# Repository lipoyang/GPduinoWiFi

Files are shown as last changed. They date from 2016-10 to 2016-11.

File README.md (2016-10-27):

GPduino WiFi
=========

## 概要
GPduino WiFiは、ESP8266搭載のWiFiラジコン制御ボードです。  
GPduinoに関する詳細は、[GPduinoサポートページ](http://lipoyang.net/gpduino)をごらんください。  
GPduinoWiFiの回路/基板設計データとプリセットファームウェアのソースをここに公開します。

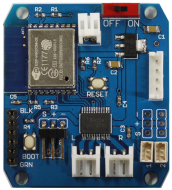
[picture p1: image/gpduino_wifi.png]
GPduinoWiFiの写真
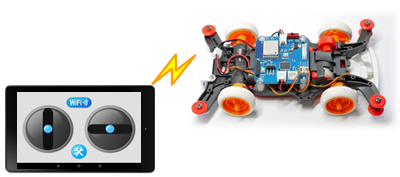
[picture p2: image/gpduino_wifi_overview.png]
概要の図
　　　　　

## ファイル一覧

* firm/GPduinoWiFi/ : ファームウェア(ESP8266のArduinoスケッチ)
* hard/GPduinoWiFi/
	* GPduinoWiFi.sch/brd: 回路/基板設計データ(Eagle形式)
	* GPduinoWiFi.pdf: 回路図(PDF)
	* GPduinoWiFi_BOM.xlsx: BOMリスト(Excel形式)
	* GPduinoWiFi.GBL/GBO/GBP/GBS/GML/GTL/GTO/GTP/GTS/TXT: ガーバデータ
* LICENSE: Apache Licence 2.0です。
	* ただし、回路/基板設計は、Creative Commons Attribution Share-Alike 3.0です。
* README.md これ

## ファームウェアの書き込み
GPduino WiFi はESP8266を搭載しており、Arduinoでファームウェアを開発できます。

* 書き込みには、USBシリアル変換基板が必要です。CN11に接続してください。
	* SparkFun製 FTDI Basic Breakout - 3.3V を推奨します。かならず、3.3Vのものを使用してください。
* まず、ArduinoIDE をインストールしておきます。 (ここでは 1.6.9 を使用)
* [ファイル] > [環境設定] > [Additional Boards Manager URLs:]に下記URLをコピペ
	* http://arduino.esp8266.com/stable/package_esp8266com_index.json (安定版)
	* http://arduino.esp8266.com/staging/package_esp8266com_index.json (開発版)
* [ツール] > [ボード] > [ボードマネージャ] で [esp8266] をインストール
* [ツール] > [ボード] で [Generic ESP8266 Module]を選択
	* Flash Mode : QIO
	* Flash Frequency : 40MHz
	* Upload Using : Serial
	* CPU Frequency : 80MHz
	* Flash Size : 4M(3M SPIFFS)　(3MBをファイルシステムで使用 / 1MBをスケッチで使用)
	* Debug port : Disabled
	* Debug Level : None
	* Reset Method : nodemcu
	* Upload Speed : 115200
	* シリアルポート : USBシリアルのCOM番号
	* 書込装置 : USBasp
* BOOTボタン(SW3)を押し下げた状態で、RESETボタン(SW2)を押して離します。
* Uploadボタンで、ファームウェアを書き込みます。

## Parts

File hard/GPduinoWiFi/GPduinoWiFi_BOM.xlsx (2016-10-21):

GPduino WiFi BOM
基板本体
No | Reference | Part Number | Vender | Description | DNP | Qty | Unit Price | Price | Lot Size | Supplier | Supplier Code
1 | C1,2 | 47u(3216) | (generic) | 3216型 |  | 2 | 30 | 60 | 10 | 秋月 | P-06040
2 | C3,4,5 | 0.1u(1608) | (generic) | 1608型 |  | 3 | 0.325 | 0.975 | 4000 | 秋月 | P-01299
3 | CN1,2 | S2B-EH | JST | EH 2極 L型ポスト | DNP | 0 | 16 | 0 | 1 | 共立 | -
4 | CN3 | S2B-PH-K-S | JST | PH 2極 L型ポスト |  | 1 | 16 | 16 | 1 | 共立 | -
5 | CN4 | B4B-EH-A | JST | EH 4極 I型ポスト | DNP | 0 | 21 | 0 | 1 | 共立 | -
6 | CN5 | 53048-0310 | Molex | PicoBlade 3極 L型ポスト | DNP (部品は付属) | 1 | 45 | 45 | 5 | RS | 319-1092
7 | CN6,7 | 53047-0310 | Molex | PicoBlade 3極 I型ポスト | DNP | 0 | 29 | 0 | 5 | RS | 319-1064
8 | CN8 | - | (generic) | ピンヘッダ 3ピン | DNP (部品は付属) | 1 | 35 | 35 | 16 | 共立 | -
9 | CN9,10 | - | (generic) | ピンヘッダ 3ピン | DNP | 0 | 17 | 0 | 12 | 共立 | -
10 | CN11 | 0 | (generic) | ピンヘッダ 6ピン I型 | DNP (部品は付属) | 1 | 70 | 70 | 8 | 共立 | -
12 | R1 | 100k(1608) | (generic) | 1608型 |  | 1 | 0.2 | 0.2 | 2500 | 秋月 | R-06104
13 | R2,3,4,5,6,7 | 10k(1608) | (generic) | 1608型 |  | 6 | 0.2 | 1.2 | 2500 | 秋月 | R-06103
14 | SW1 | SS-12SDP2 | NKK | スライドスイッチ | DNP (部品は付属) | 1 | 66 | 66 | 1 | 共立 | 391139
15 | SW2,3 | SKRPACE010 | ALPS | 表面実装タクトスイッチ |  | 2 | 20 | 40 | 5 | 秋月 | P-06185
16 | U1 | TC1262-3.3VDB05MP | Microchip | LDO, 3.3V-0.5A, SOT-223型 |  | 1 | 81 | 81 | 1 | RS | 703-7905
17 | U2 | TB6621FNG | Toshiba | Dual DCモータドライバ |  | 1 | 306 | 306 | 1 | RS | 770-3797
18 | U3 | ESP-WROOM-02 | Espressif Systems | ESP8266 WiFiモジュール |  | 1 | 550 | 550 | 1 | 秋月 | M-09607
19 | - | - | Elecrow | 基板 |  | 1 | 275.1 | 275.1 | 10 | Elecrow | -
20 | - | PH2P300L | Marutsu | PH 2極 アッセンブルケーブル |  | 1 | 54 | 54 | 1 | マルツ | -
 |  |  |  |  |  |  | Total | 1600.475

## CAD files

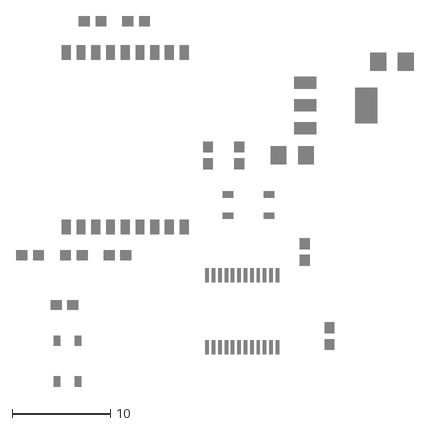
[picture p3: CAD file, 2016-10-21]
hard/GPduinoWiFi/GPduinoWiFi.dxf
40.4 x 37.7

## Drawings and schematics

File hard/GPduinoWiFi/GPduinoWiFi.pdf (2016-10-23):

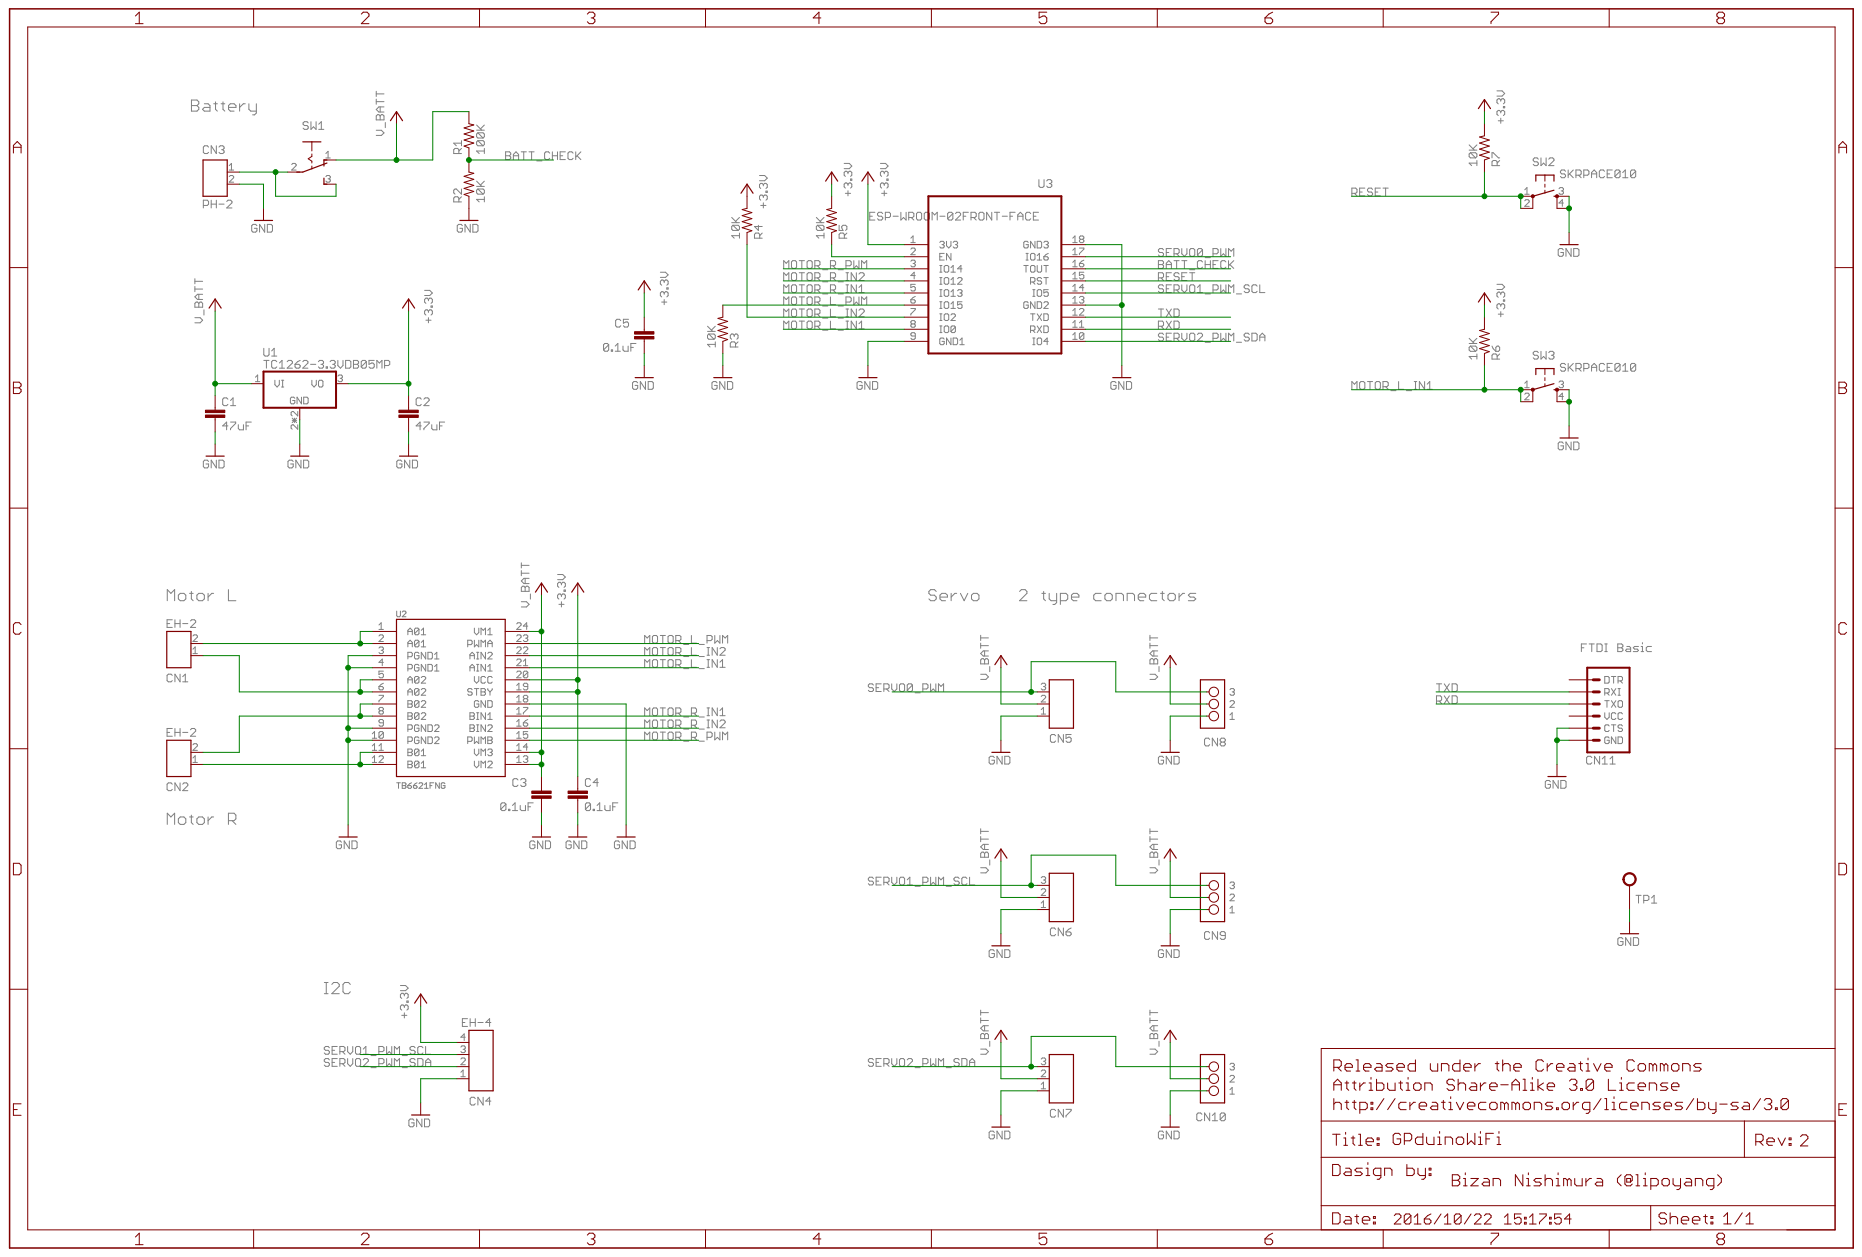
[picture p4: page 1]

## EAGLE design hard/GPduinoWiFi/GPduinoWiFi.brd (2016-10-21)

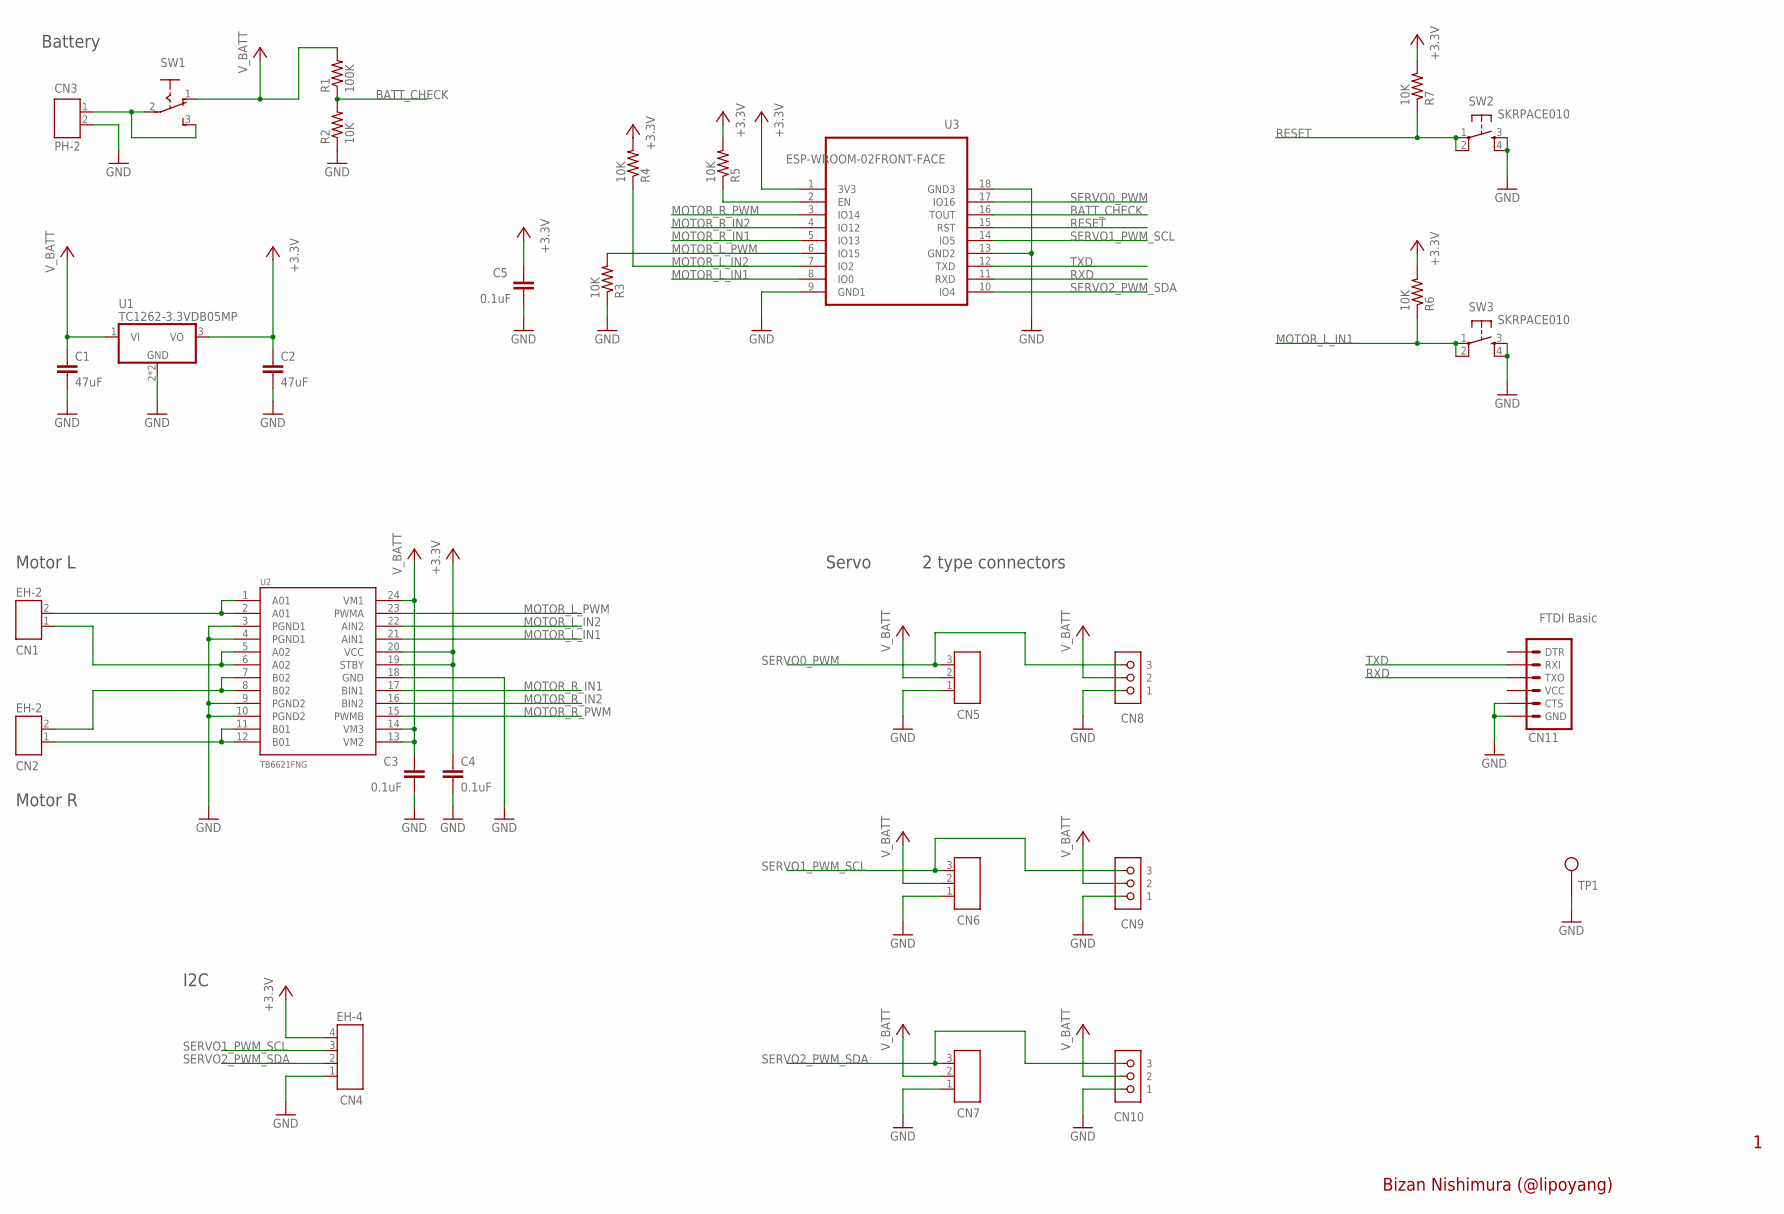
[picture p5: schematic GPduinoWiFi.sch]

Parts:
C1, C2: 47uF; C3216
C3, C4, C5: 0.1uF; C1608
CN1, CN2: EH-2
CN3: PH-2
CN4: EH-4
CN5, CN6, CN7: PICOBLADE-3
CN8, CN9, CN10: cn6; CON_RC_SERVO
CN11: FTDI Basic; 1X06
R1: 100K; 0603-RES
R2, R3, R4, R5, R6, R7: 10K; 0603-RES
SW1: SW1; SLIDE-SW
SW2, SW3: SKRPACE010
TP1: TEST_PIN
U1: TC1262-3.3VDB05MP; SOT223
U2: TB6621FNG; SSOP24
U3: ESP-WROOM-02FRONT-FACE; FRONT-FACE

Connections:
+3V3: C2.1, C4.1, C5.1, CN4.4, R4.2, R5.2, R6.2, R7.2, U1.3 (VO), U2.19 (STBY), U2.20 (VCC), U3.1 (3V3)
A01: CN1.2, U2.1 (A01), U2.2 (A01)
A02: CN1.1, U2.5 (A02), U2.6 (A02)
BATT_CHECK: R1.1, R2.2, U3.16 (TOUT)
GND: C1.2, C2.2, C3.2, C4.2, C5.2, CN3.2, CN4.1, CN5.1, CN6.1, CN7.1, CN8.1, CN9.1, CN10.1, CN11.5 (CTS), CN11.6 (GND), R2.1, R3.1, SW2.3, SW2.4, SW3.3, SW3.4, TP1.1, U1.2 (GND), U1.4 (GND), U2.3 (PGND1), U2.4 (PGND1), U2.9 (PGND2), U2.10 (PGND2), U2.18 (GND), U3.9 (GND1), U3.13 (GND2), U3.18 (GND3)
MOTOR_L_IN1: R6.1, SW3.1, SW3.2, U2.21 (AIN1), U3.8 (IO0)
MOTOR_L_IN2: R4.1, U2.22 (AIN2), U3.7 (IO2)
MOTOR_L_PWM: R3.2, U2.23 (PWMA), U3.6 (IO15)
MOTOR_R_IN1: U2.17 (BIN1), U3.5 (IO13)
MOTOR_R_IN2: U2.16 (BIN2), U3.4 (IO12)
MOTOR_R_PWM: U2.15 (PWMB), U3.3 (IO14)
unnamed: CN3.1, SW1.2, SW1.3 (S)
unnamed: R5.1, U3.2 (EN)
unnamed: CN2.1, U2.11 (B01), U2.12 (B01)
unnamed: CN2.2, U2.7 (B02), U2.8 (B02)
RESET: R7.1, SW2.1, SW2.2, U3.15 (RST)
RXD: CN11.3 (TXO), U3.11 (RXD)
SERVO0_PWM: CN5.3, CN8.3, U3.17 (IO16)
SERVO1_PWM_SCL: CN4.3, CN6.3, CN9.3, U3.14 (IO5)
SERVO2_PWM_SDA: CN4.2, CN7.3, CN10.3, U3.10 (IO4)
TXD: CN11.2 (RXI), U3.12 (TXD)
V_BATT: C1.1, C3.1, CN5.2, CN6.2, CN7.2, CN8.2, CN9.2, CN10.2, R1.2, SW1.1 (O), U1.1 (VI), U2.13 (VM2), U2.14 (VM3), U2.24 (VM1)

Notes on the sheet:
Battery
Servo
Motor L
Bizan Nishimura (@lipoyang)
2 type connectors
Motor R
I2C

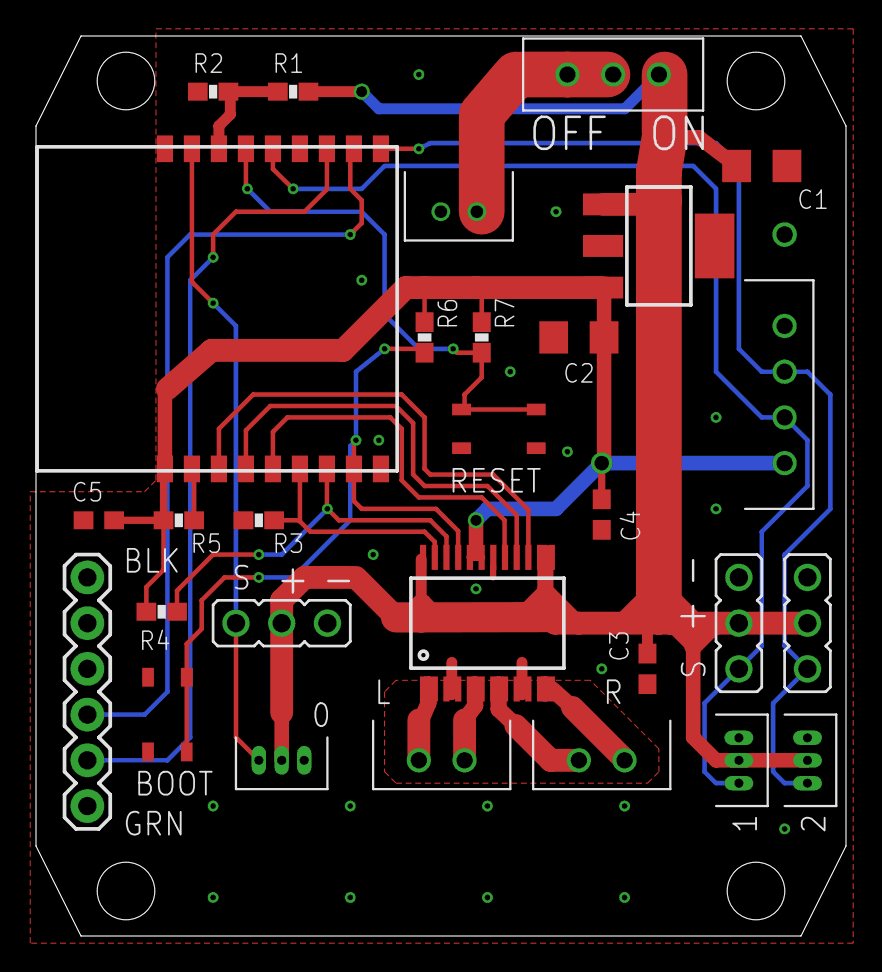
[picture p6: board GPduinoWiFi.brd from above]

Board: 2 copper layers, 45.0 x 50.0 mm, 30 parts (0 on the bottom side), 22 nets.

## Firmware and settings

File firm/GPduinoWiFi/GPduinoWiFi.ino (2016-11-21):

#include <Servo.h>
#include <EEPROM.h>
extern "C" {
#include "user_interface.h"
}
#include "common.h"
#include "MovingAverage.h"
#include "UdpComm.h"

// UDP通信クラス
UdpComm udpComm;
// UDP受信コールバック
void udpComm_callback(char* buff);

// ピン番号 (デジタル)
#define MOTOR_R_PWM    14
#define MOTOR_R_IN2    12
#define MOTOR_R_IN1    13
#define MOTOR_L_PWM    15
#define MOTOR_L_IN2    2
#define MOTOR_L_IN1    0
#define SERVO0_PWM     16
#define SERVO1_PWM     5
#define SERVO2_PWM     4

// サーボ
Servo servo[3];

// バッテリー電圧チェック
MovingAverage Vbat_MovingAve;

// モード
static int drive_mode;
#define MODE_TANK   0   // 戦車モード
#define MODE_CAR    1   // 自動車モード

// 戦車モードのプロポ状態保持用
static int g_fb;  // 前後方向
static int g_lr;  // 左右方向

// 暴走チェックカウンタ
static int cnt_runaway;

// 3.5V未満でローバッテリーとする
// (3.5V / 11) / 1.0V * 1024 =  325
#define LOW_BATTERY    325

// 四輪操舵のモード
static int g_steer_pol_f;
static int g_steer_pol_b;

// サーボの調整
static int g_servo_pol[3]; // 極性
static int g_servo_ofs[3]; // オフセット
static int g_servo_amp[3]; // 振幅

// 送信バッファ
static char txbuff[256];

/**
 * バッテリー電圧チェック
 */
void battery_check()
{
    if(!udpComm.isReady()) return;
    
    static int cnt1 = 0;
    static int cnt2 = 0;
    
    // 100msecごとに電圧値測定
    cnt1++;
    if(cnt1 < 100) return;
    cnt1 = 0;

    unsigned short Vbat = system_adc_read();
    unsigned short Vbat_ave = Vbat_MovingAve.pop(Vbat);
    //Serial.print("Vbat_ave");Serial.println(Vbat_ave);

    // 1秒ごとに電圧値送信
    cnt2++;
    if(cnt2 >= 10)
    {
        cnt2=0;
        
        txbuff[0]='#';
        txbuff[1]='B';
        Uint16ToHex(&txbuff[2], Vbat_ave, 3);
        txbuff[5]='$';
        txbuff[6]='\0';
        udpComm.send(txbuff);
    }
    
    // 電圧が低下したら停止
    if(Vbat_ave < LOW_BATTERY){
        // モータ停止
        analogWrite(MOTOR_L_PWM, 0);
        analogWrite(MOTOR_R_PWM, 0);
        digitalWrite(MOTOR_L_IN1, LOW);
        digitalWrite(MOTOR_L_IN2, LOW);
        digitalWrite(MOTOR_R_IN1, LOW);
        digitalWrite(MOTOR_R_IN2, LOW);
        // 復帰しない
        while(true){
            ;
        }
    }
}

/**
 * 暴走チェック
 */
void runaway_check()
{
    cnt_runaway++;
    
    // 1秒間コマンドが来なければモータ停止
    if(cnt_runaway > 1000)
    {
      analogWrite(MOTOR_L_PWM, 0);
      analogWrite(MOTOR_R_PWM, 0);
      digitalWrite(MOTOR_L_IN1, LOW);
      digitalWrite(MOTOR_L_IN2, LOW);
      digitalWrite(MOTOR_R_IN1, LOW);
      digitalWrite(MOTOR_R_IN2, LOW);
    }
}

/*
 * サーボの初期化, モードの設定
 */
void servo_init()
{
    int i;
    if(EEPROM.read(0) == 0xA5){
        for(i=0;i<3;i++){
            g_servo_pol[i] = (int)((signed char)EEPROM.read(i*3 + 1));
            g_servo_ofs[i] = (int)((signed char)EEPROM.read(i*3 + 2));
            g_servo_amp[i] =                    EEPROM.read(i*3 + 3);
        }
        drive_mode = EEPROM.read(10);
        if(drive_mode == MODE_TANK){
            Serial.println("TANK MODE");
        }else{
            Serial.println("CAR MODE");
        }
        
    }else{
        EEPROM.write(0, 0xA5);
        for(i=0;i<3;i++){
            g_servo_pol[i] = 1;
            g_servo_ofs[i] = 0;
            g_servo_amp[i] = 90;
            EEPROM.write(i*3 + 1, g_servo_pol[i]);
            EEPROM.write(i*3 + 2, g_servo_ofs[i]);
            EEPROM.write(i*3 + 3, g_servo_amp[i]);
        }
        drive_mode = MODE_CAR;
        EEPROM.write(10, drive_mode);
        EEPROM.commit();
    }
    servo[0].attach(SERVO0_PWM);
    servo[1].attach(SERVO1_PWM);
    servo[2].attach(SERVO2_PWM);
    servo_ctrl(0,0);
    servo_ctrl(1,0);
    servo_ctrl(2,0);
}

/*
 * サーボ制御
 */
void servo_ctrl(int ch, int val)
{
    int deg = 90 + ((val + g_servo_ofs[ch]) *  g_servo_amp[ch]) / 127 * g_servo_pol[ch];
    
    // sprintf(txbuff, "%4d %4d / %4d %4d %4d", val, deg, g_servo_ofs[ch], g_servo_amp[ch], g_servo_pol[ch]);
    // Serial.println(txbuff);
    
    servo[ch].write(deg);
}

// 初期設定
void setup() {
    Serial.begin(115200);
    delay(100);
    
    // EEPROMの初期化
    EEPROM.begin(128); // 128バイト確保
    
    // UDP通信の設定
    udpComm.beginAP(NULL, "12345678");
    //udpComm.beginSTA("SSID", "password", "gpduino");
    udpComm.onReceive = udpComm_callback;

    // PWMの初期化
    analogWrite(MOTOR_L_PWM, 0);
    analogWrite(MOTOR_R_PWM, 0);
    
    // GPIOの初期化
    digitalWrite(MOTOR_L_IN1, LOW);
    digitalWrite(MOTOR_L_IN2, LOW);
    digitalWrite(MOTOR_R_IN1, LOW);
    digitalWrite(MOTOR_R_IN2, LOW);
    pinMode(MOTOR_L_IN1, OUTPUT);
    pinMode(MOTOR_L_IN2, OUTPUT);
    pinMode(MOTOR_R_IN1, OUTPUT);
    pinMode(MOTOR_R_IN2, OUTPUT);
    
    // モード判定
    //int mode_check = analogRead( MODE_CHECK );
    //drive_mode = (mode_check > 512) ? MODE_CAR : MODE_TANK;
    
    //if(drive_mode == MODE_CAR){
        // サーボの初期化, モード設定
        servo_init();
    //}
    
    // 変数初期化
    g_fb = 0;
    g_lr = 0;
    cnt_runaway = 0;
    Vbat_MovingAve.init();
    g_steer_pol_f = 1;
    g_steer_pol_b = 0;
}

// メインループ
void loop() {
    
    // UDP通信
    udpComm.loop();
    // バッテリー電圧チェック
    battery_check();
    // 暴走チェック
    runaway_check();
    
    delay(1);
}

/*
 * モータの制御
 */
void ctrl_motor(int ch, int val)
{
    static const int IN1[]={MOTOR_L_IN1, MOTOR_R_IN1};
    static const int IN2[]={MOTOR_L_IN2, MOTOR_R_IN2};
    static const int PWM[]={MOTOR_L_PWM, MOTOR_R_PWM};
    
    int l,r;
    int lpwm,rpwm,lin1,lin2,rin1,rin2;
    
    int pwm = (abs(val) << 1) + 1;
    if(pwm<0) pwm = 0;
    if(pwm>255) pwm = 255;
    
    int in1,in2;
    if(val > 0){
        in1 = LOW;
        in2 = HIGH;
    }else if(val < 0){
        in1 = HIGH;
        in2 = LOW;
    }else{
        in1 = LOW;
        in2 = LOW;
        pwm = 0;
    }

    digitalWrite(IN1[ch], in1);
    digitalWrite(IN2[ch], in2);
    analogWrite(PWM[ch], pwm*4);
}

/**
 * 戦車のモータ制御
 */
void ctrl_tank()
{
    int l,r;
    int lpwm,rpwm,lin1,lin2,rin1,rin2;
    
    r = (int)(g_fb - g_lr/2);
    l = (int)(g_fb + g_lr/2);
    
    // sprintf(txbuff, "%4d %4d %4d %4d", l, r, g_fb, g_lr);
    // Serial.println(txbuff);
    
    ctrl_motor(0, l);
    ctrl_motor(1, r);
}

/**
 * 受信したコマンドの実行
 *
 * @param buff 受信したコマンドへのポインタ
 */
void udpComm_callback(char* buff)
{
    unsigned short val;
    int sval, sval2;
    int deg;
    int ch;
    int i;
    
    cnt_runaway = 0; // 暴走チェックカウンタのクリア
    
    Serial.print("udpComm_callback:");Serial.println(buff);
    
    if(buff[0] != '#') return;
    buff++;
    
    switch(buff[0])
    {
    /* Dコマンド(前進/後退)
       書式: #Dxx$
       xx: 0のとき停止、正のとき前進、負のとき後退。
     */
    case 'D':
        // 値の解釈
        if( HexToUint16(&buff[1], &val, 2) != 0 ) break;
        sval = (int)((signed char)val);
        
        // 自動車モードの場合
        if(drive_mode == MODE_CAR)
        {
            ctrl_motor(0, sval);
            ctrl_motor(1, sval);
        }
        // 戦車モードの場合
        else
        {
            g_fb = sval;
            ctrl_tank();
        }
        break;
        
    /* Tコマンド(旋回)
       書式: #Txxn$
       n: 4WSモード。0のとき後輪固定、1のとき同相、2のとき逆相
       xx: 0のとき中立、正のとき右旋回、負のとき左旋回
     */
    case 'T':
        // 4WSモード
        switch(buff[3]){
        case '0':// FRONT
            g_steer_pol_f = 1;
            g_steer_pol_b = 0;
            break;
        case '1':// COMMON
            g_steer_pol_f = 1;
            g_steer_pol_b = 1;
            break;
        case '2':// REVERSE
            g_steer_pol_f = 1;
            g_steer_pol_b = -1;
            break;
        case '3':// REAR
            g_steer_pol_f = 0;
            g_steer_pol_b = 1;
            break;
        default:
            g_steer_pol_f = 1;
            g_steer_pol_b = 0;
            break;
        }
        // 値の解釈
        if( HexToUint16(&buff[1], &val, 2) != 0 ) break;
        sval = (int)((signed char)val);
        
        // 自動車モードの場合
        if(drive_mode == MODE_CAR)
        {
            servo_ctrl(0, sval);
            servo_ctrl(1, g_steer_pol_f * sval);
            servo_ctrl(2, g_steer_pol_b * sval);
        }
        // 戦車モードの場合
        else
        {
            g_lr = sval;
            ctrl_tank();
        }
        break;
        
    /* Mコマンド(モータ制御)
       書式1: #Mnxx$
       n: '1'はモータ1(左)、'2'はモータ2(右)
       xx: 0のとき停止、正のとき正転、負のとき反転
       
       書式2: #MAxxyy$
       xx: モータ1(左)  0のとき停止、正のとき正転、負のとき反転
       yy: モータ2(右)  0のとき中立、正のとき正転、負のとき反転
     */
    case 'M':
        switch(buff[1]){
        case '1':
            // 値の解釈
            if( HexToUint16(&buff[2], &val, 2) != 0 ) break;
            sval = (int)((signed char)val);
            ctrl_motor(0, sval);
            break;
        case '2':
            // 値の解釈
            if( HexToUint16(&buff[2], &val, 2) != 0 ) break;
            sval = (int)((signed char)val);
            ctrl_motor(1, sval);
            break;
        case 'A':
            // 値の解釈
            if( HexToUint16(&buff[2], &val, 2) != 0 ) break;
            sval = (int)((signed char)val);
            if( HexToUint16(&buff[4], &val, 2) != 0 ) break;
            sval2 = (int)((signed char)val);
            ctrl_motor(0, sval);
            ctrl_motor(1, sval2);
            break;
        }
        break;
        
    /* Sコマンド(サーボ制御)
       書式: #Sxxn$
       xx: 0のとき中立、正のとき正転、負のとき反転
       n: サーボチャンネル 0～2
     */
    case 'S':
        // 値の解釈
        if( HexToUint16(&buff[1], &val, 2) != 0 ) break;
        sval = (int)((signed char)val);
        // チャンネル
        ch = (buff[3] == '1') ? 1 : ((buff[3] == '2') ? 2 : 0);
        // サーボの制御
        servo_ctrl(ch, sval);
        break;
        
    /* Aコマンド(サーボの調整)
        (1)サーボ極性設定
           書式: #APxn$
           n: サーボチャンネル 0～2
           xは'+'または'-'。'+'は正転、'-'は反転。初期値は正転。
        (2)サーボオフセット調整
           書式: #AOxxn$
           n: サーボチャンネル 0～2
           xx:中央位置のオフセット
        (3)サーボ振幅調整
           書式: #AAnxx$
           n: サーボチャンネル 0～2
           xx:振れ幅
        (4)サーボ設定値保存
           書式: #AS$
           サーボの設定値をEEPROMに保存する
        (5)サーボ設定値読み出し
            書式: #AL$
           サーボの設定値をEEPROMから読み出し、送信する
     */
    case 'A':
        switch(buff[1]){
        case 'P':
            ch = (buff[3] == '1') ? 1 : ((buff[3] == '2') ? 2 : 0);
            if(buff[2] == '+'){
                g_servo_pol[ch] = 1;
            }else if(buff[2] == '-'){
                g_servo_pol[ch] = -1;
            }
            break;
        case 'O':
            ch = (buff[4] == '1') ? 1 : ((buff[4] == '2') ? 2 : 0);
            // 値の解釈
            if( HexToUint16(&buff[2], &val, 2) != 0 ) break;
            g_servo_ofs[ch] = (int)((signed char)val);
            break;
        case 'A':
            ch = (buff[4] == '1') ? 1 : ((buff[4] == '2') ? 2 : 0);
            // 値の解釈
            if( HexToUint16(&buff[2], &val, 2) != 0 ) break;
            g_servo_amp[ch] = (int)((unsigned char)val);
            break;
        case 'S':
            for(i=0;i<3;i++){
                EEPROM.write(i*3 + 1, g_servo_pol[i]);
                EEPROM.write(i*3 + 2, g_servo_ofs[i]);
                EEPROM.write(i*3 + 3, g_servo_amp[i]);
            }
            EEPROM.write(10, drive_mode);
            EEPROM.commit();
            break;
        case 'L':
            txbuff[0]='#';
            txbuff[1]='A';
            txbuff[2]='L';
            for(i=0;i<3;i++){
                g_servo_pol[i] = (int)((signed char)EEPROM.read(i*3 + 1));
                g_servo_ofs[i] = (int)((signed char)EEPROM.read(i*3 + 2));
                g_servo_amp[i] =                    EEPROM.read(i*3 + 3);
                txbuff[3+i*5] = (g_servo_pol[i]==1) ? '+' : '-';
                Uint16ToHex(&txbuff[4+i*5], (unsigned short)((unsigned char)g_servo_ofs[i]), 2);
                Uint16ToHex(&txbuff[6+i*5], (unsigned short)(               g_servo_amp[i]), 2);
            }
            txbuff[18]='$';
            txbuff[19]='\0';
            udpComm.send(txbuff);
            break;
        }
        break;
        
    /* Vコマンド(車両モードの設定)
        (1)自動車モードに設定
           書式: #VC$
        (2)戦車モードに設定
           書式: #VT$
        (3)車両モードの読み出し
           書式: #VL$
     */
    case 'V':
        switch(buff[1]){
        case 'C':
            drive_mode = MODE_CAR;
            //EEPROM.write(10, drive_mode);
            //EEPROM.commit();
            break;
        case 'T':
            drive_mode = MODE_TANK;
            //EEPROM.write(10, drive_mode);
            //EEPROM.commit();
            break;
        case 'L':
            txbuff[0]='#';
            txbuff[1]='V';
            txbuff[2]= (drive_mode == MODE_TANK) ? 'T' : 'C';
            txbuff[18]='$';
            txbuff[19]='\0';
            udpComm.send(txbuff);
            break;
        }
        break;
    }
}

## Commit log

2016-10-21 ・ファームウェアのソースを追加
2016-10-21 ・基板のCADデータを追加
    [GPduinoWiFi.GBL, GPduinoWiFi.GBO, GPduinoWiFi.GBP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]
2016-10-23 ・回路図の修正（リビジョン番号のみ）
    [GPduinoWiFi.sch]
2016-10-23 ・READMEの記述
2016-10-27 ・車両モード設定機能の追加
2016-10-27 ・READMEの修正
2016-11-21 ・モータ出力のバグ修正

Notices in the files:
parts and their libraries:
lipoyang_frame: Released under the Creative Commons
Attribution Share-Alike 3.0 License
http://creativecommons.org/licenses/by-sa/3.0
